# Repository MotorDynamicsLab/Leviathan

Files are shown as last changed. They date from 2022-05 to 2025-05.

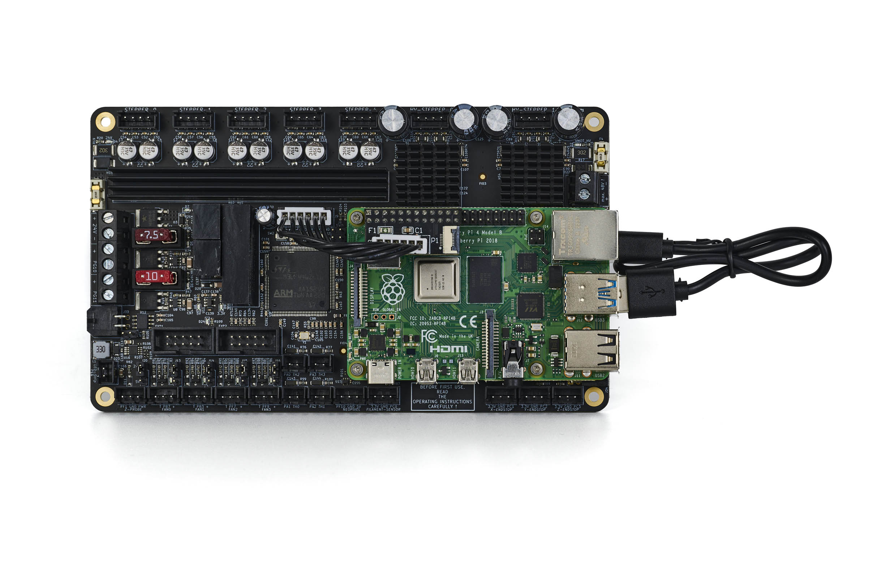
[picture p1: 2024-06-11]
Media/rpi4_usb_installed.jpg

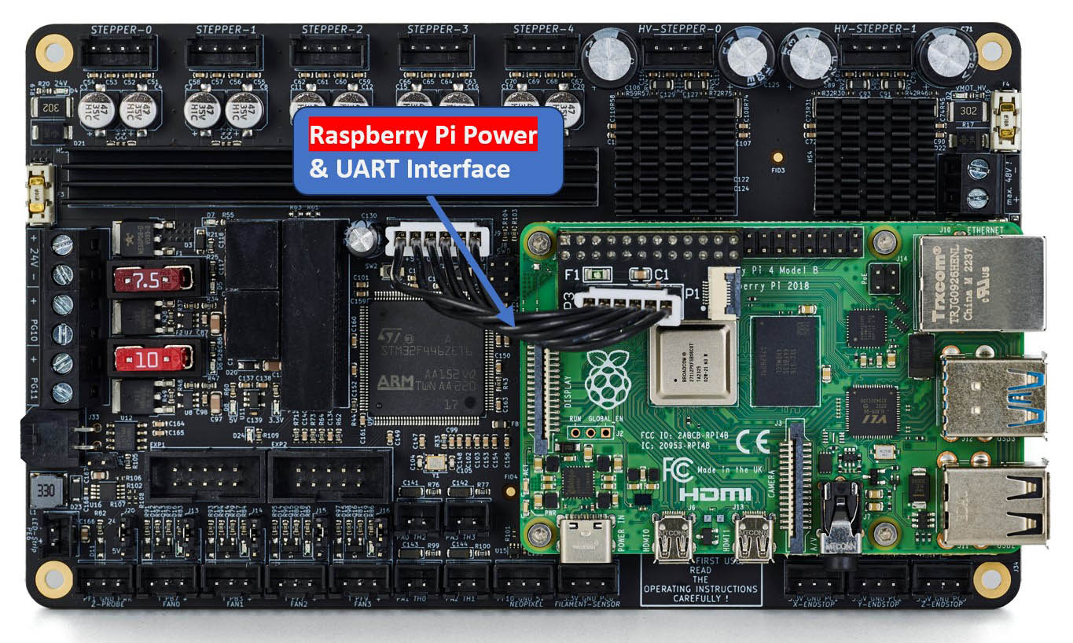
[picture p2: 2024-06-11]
Media/rpi4_installed_UART_labels.jpg

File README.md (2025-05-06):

Leviathan_Mainboard Leviathan Mainboard

# Voron Leviathan
Voron Leviathan is collaboration between JNP and the team at LDO to create a controller board specific for the needs of Voron 3D printers. It features: 
- STM32F446 Microcontroller at 180Mhz clock speed. 
- Reverse polarity protection for main power supply and HV Stepper supply input
- Superior stepper driver cooling (passive)
- Dedicated mounting space for a Raspberry Pi 3,4,5 or Zero 2W
- Dedicated power supply and uart port for Raspberry Pi
- 5x Integrated TMC2209 stepper drivers. 
- 2x Integrated 48V rated TMC5160 stepper drivers. 
- 4x Fan ports with flyback protection, 5V/24V selectable voltage, and tachometer inputs. 
- 4x Thermistor ports with 2k2 ohm pullup resistors. 
- 1x Dedicated LED strip with flicker free dimming down to 1%.
- 1x Neopixel port.
- 1x Hotend power output up to 180W. 
- 1x Hotbed power output up to 240W
- 1x Dedicated Z probe port with selectable voltage and integrated diode.
- 3x Endstop ports and a filament sensor port 

## Setup Guide
https://ldomotion.com/p/guide/VORON-Leviathan-V12

## Electrical Specifications
| Parameter | Symbol |  Min  | Typ | Max | Unit | Comments |
| --- | --- | ----- | ----- | ----- |----- | --- |
| Main Supply Voltage | V<sub>in</sub> | 18 | 24 | 28 |  V | Supply voltage for the entire PCB except for HV stepper drivers |
| HV Stepper Supply Voltage | V<sub>HV</sub> | 24 | 48 | 55 |  V | Supply voltage for the HV stepper drivers |
| RPi Supply Out | I<sub>RPI</sub> | | | 3 |  A | Current rating of Raspberry Power supply output |
| Hotend Current | I<sub>he</sub> | | | 7.5 |  A | Current rating of hotend channel |
| Heatbed Current | I<sub>hb</sub> | | | 10 |  A | Current rating of heatbed channel |
| Fan Current | I<sub>fan</sub> | | | 0.5 |  A | Current rating per fan channel |
| Stepper Current | I<sub>mot</sub> | | | 2 |  A | Current rating of each TMC2209 stepper channel |
| HV Stepper Current | I<sub>hv_mot</sub> | | | 3 |  A | Current rating of each TMC5160 stepper driver |
| Neopixel Current | I<sub>rgb</sub> | | | 0.5 |  A | Current rating Neopixel port |
| LED-Strip Current | I<sub>led</sub> | | 0.35  | |  A | Current rating of LED strip |
| Endstop IO Level | V<sub>stop</sub> | | 3.3 | 5.0 |  V | Logic level of endstop input |
| Filament Sensor IO Level  | V<sub>fil</sub> | | 3.3 | 5.0 |  V | Logic level of filament sensor input |

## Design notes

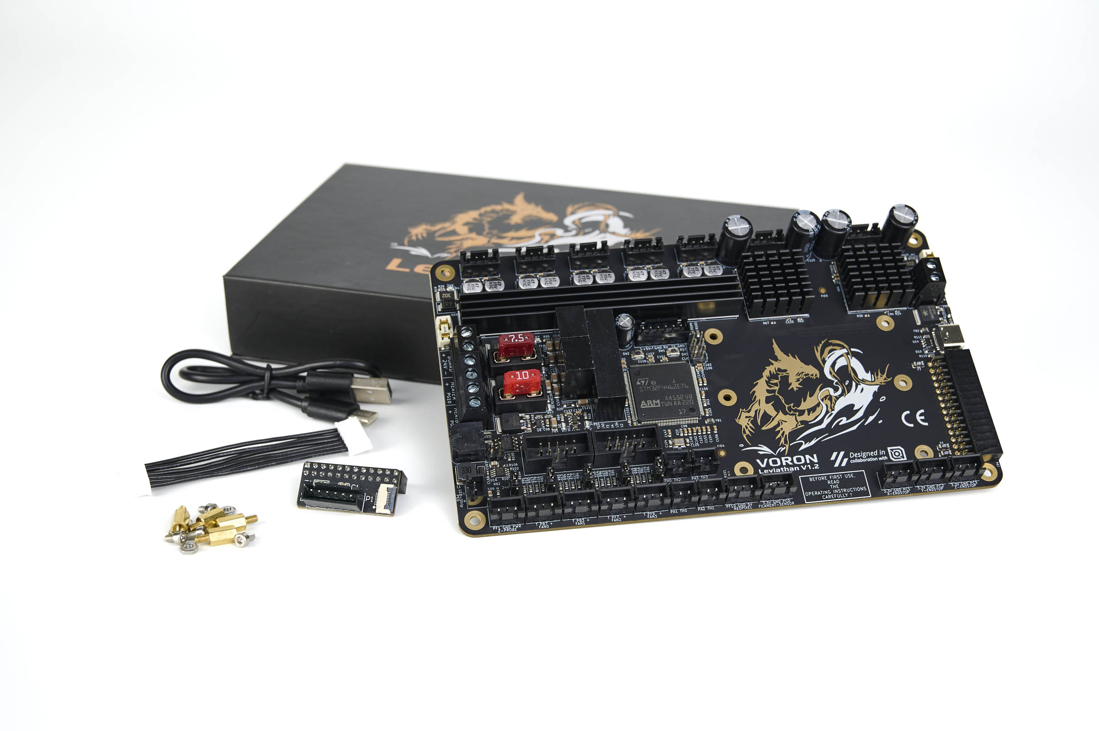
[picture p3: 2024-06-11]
Media/overview.jpg

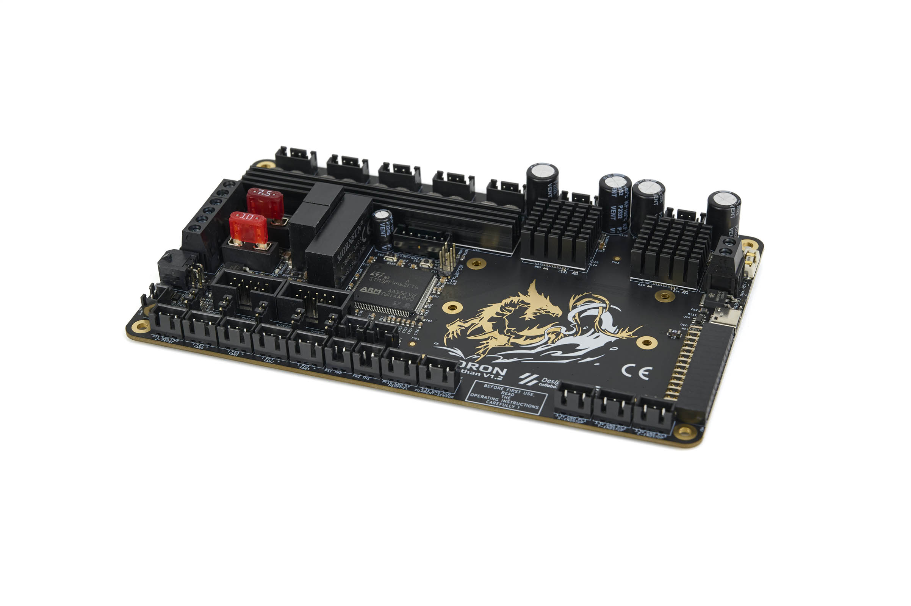
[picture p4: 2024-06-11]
Media/perspective_view.jpg

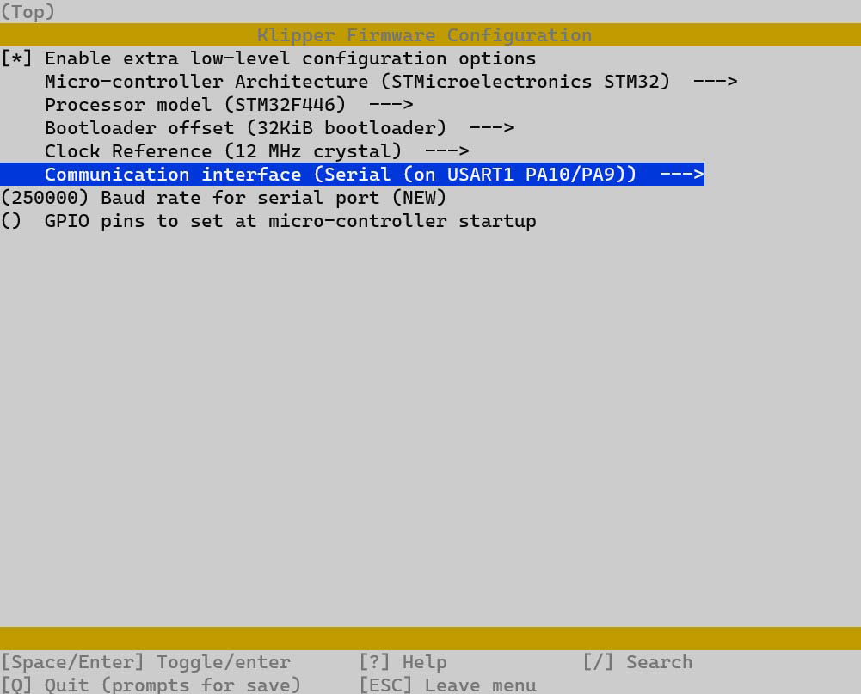
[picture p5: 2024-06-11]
Media/klipper_uart.jpg

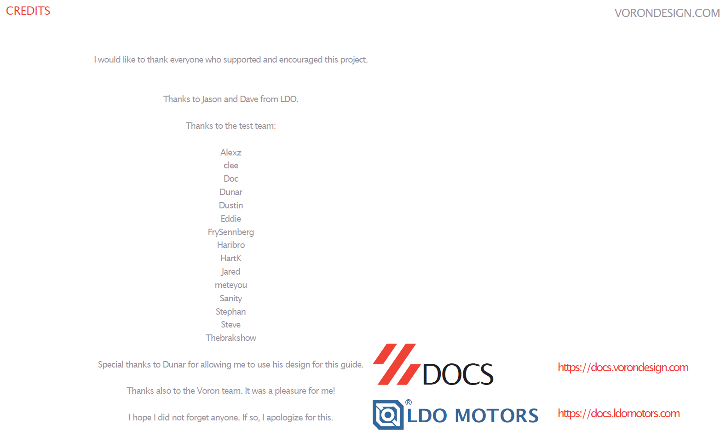
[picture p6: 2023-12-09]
Media/credits.png

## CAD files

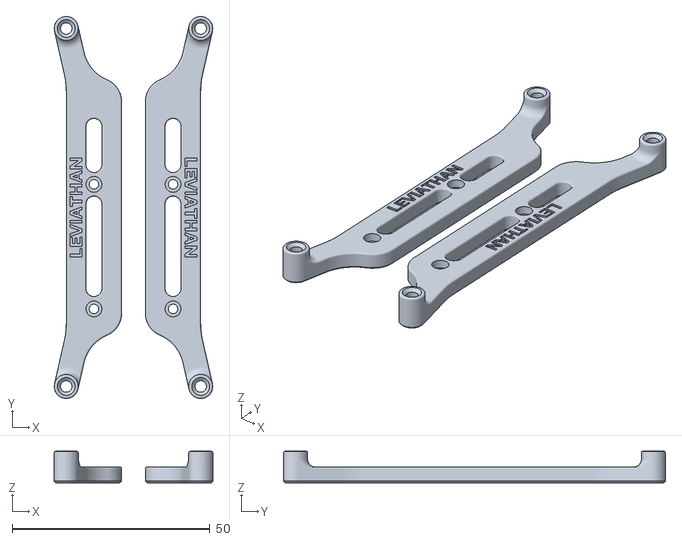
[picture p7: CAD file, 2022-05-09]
STLs/Leviathan_bracket_set.stl
40.1 x 96.6 x 8.00

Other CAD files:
STLs/Leviathan_bracket_set.f3d

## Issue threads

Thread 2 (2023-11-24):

Marlin source

thisiskeithb, 2023-11-24:
Hello!

Keith here from the [Marlin Firmware team](https://github.com/MarlinFirmware/Marlin).

Jason was kind enough to ship over one of these Leviathan boards to add Marlin support, but starting from scratch is fairly involved and I was hoping to collect some more information/files from a board developer. I can create the required pins file based on the [Klipper configs hosted within this repo](https://github.com/MotorDynamicsLab/Leviathan/tree/master/Firmware) and labeling on the board, but I don't have the PlatformIO variant files or build environment details which are crucial to getting it up and running.

We have a few boards with an `STM32F446ZET6` MCU, namely the BTT Octopus Pro V1.0, so I planned to copy those variant files over as a starting point just to see if I can get it going, but I doubt it'll be that easy 😄.

As an example of what I'm after, [here's a PR I put into Marlin](https://github.com/MarlinFirmware/Marlin/pull/23008/files) adding support for a board. These files in particular would be helpful:
- `buildroot/share/PlatformIO/boards/<board>.json`
- `buildroot/share/PlatformIO/variants/<variant>/*`
- Variant details in `ini/stm32f4.ini`.

If you have a working Marlin source, I can get that prepped & ported upstream, but any info would be greatly appreciated!

JNP-1, 2023-11-24:
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

Nice to have you here. I'll have a look at it. I have to set up PlatformIO first.
To be honest, I haven't done anything with Marlin for a long time.
But it shouldn't be a problem.

thisiskeithb, 2023-11-25:
I'm going to close this issue since @meteyou submitted a PR and we're working through the required changes.

Thanks!

Closed 2023-11-25.

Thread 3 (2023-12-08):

Manual Diagram Out of Date (Page 13)

ChrisWhite1985, 2023-12-08:
Please can you update the manual on page 13 to show the latest PCB layout.

Also can you share the PCB Socket Types so we can acquire the correct plugs and include how best to connect the board to RPI?

JNP-1, 2023-12-11:
> Please can you update the manual on page 13 to show the latest PCB layout.
>
> Also can you share the PCB Socket Types so we can acquire the correct plugs and include how best to connect the board to RPI?

Page 13 already shows the current layout (V1.2).
All sockets are of the JST-XH type.
A ready-made cable with adapter board is already included for the Pi power supply.
It is also described here with pictures in the Raspberry Pi Mounting section.
https://www.ldomotion.com/p/guide/VORON-Leviathan-V12

ChrisWhite1985, 2023-12-11:
Ah I can see that Page 13 shows a Raspberry Pi installed on the Leviathan which is where my confusion started. This should be made clear i.e. "Leviathan V1.2 with Raspberry Pi 4 Model B installed". As RPI is not included with the Leviathan board and requires the user to install it seperately?

JNP-1, 2023-12-11:
> Ah I can see that Page 13 shows a Raspberry Pi installed on the Leviathan which is where my confusion started. This should be made clear i.e. "Leviathan V1.2 with Raspberry Pi 4 Model B installed". As RPI is not included with the Leviathan board and requires the user to install it seperately?

To be honest, page 13 is all about the dimensions.
Mounting material is included with the board, the RPi must be installed by the user.

ChrisWhite1985, 2023-12-11:
Sure, having seen the above link with information on how the RPI mounts its much clearer. What type of plug is the CANBUS port as well please, I think this is also not indicated?

Closed 2023-12-11.

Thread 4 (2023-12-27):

no 12v supply for fan headers

TheRealDeathsneeze, 2023-12-27:
The general selection for fans in 12v is much better than with 24v.  Other contemporary boards support 12v  fans. Leviathan should too.

kingnoob1377, 2023-12-28:
Yes, 12V fans are much more common, so not having any 12V port is such a bummer.

JNP-1, 2024-01-02:
Is this about a specific use case?

TheRealDeathsneeze, 2024-01-04:
yes. 12v fans that are not available in 24v or 5v variants. specifically 1U server fans.

JNP-1, 2024-01-05:
424J/2HP from ebmpast are 24V 1U server fans.
https://www.ebmpapst.com/de/en/products/axial-fans/p/424JH.html

TheRealDeathsneeze, 2024-01-10:
I wasnt aware of that option, however it's fairly low flow and somewhat low temperature rating.

a 12v option on the board would open up the selection for fans greatly. Would love to see it on a revision of the board

JNP-1, 2024-01-10:
May I ask what you want to do with a high flow fan on a printer?

CallumRD1, 2024-02-02:
I also miss the 12V fan option on the Leviathan. I have a stash of 12V Noctua electronics fans that I use on printers and the best 4010 part cooling fans for Xol or Blackbird/Archetype toolheads are 12V.

JNP-1, 2024-02-07:
Noctua now also has 24V. Another option would be to use a 24V fan and throttle it via PWM.

CallumRD1, 2024-02-07:
While many 24V fans do exist, that doesn’t remove the utility of having a 12V option. I’m currently forced to run 12V buck converters to get my 12V part cooling and electronics fans to run on Leviathan. It was so much more convenient in my octopus where I could just select 12V output. And these fans don’t exist in 24V configurations, so even if I wanted to replace ~$100 in fans for native Leviathan support, I couldn’t. It’s really obnoxious that such a simple and useful feature was omitted from this board.

JNP-1, 2024-02-07:
The decision did not come from me.

TheRealDeathsneeze, 2024-02-07:
> Adding an option to use 12V could be very simple, assuming 12V is available already and the real-estate on the PCB is available as well. Mellow does it with the Fly Super8 too.

Not to mention since the board has 5160s built in, there needs to be a 12v source on the board anyways.

JNP-1, 2024-02-07:
If someone short-circuits these 12V because a fan is defective, the TMC5160 would also be destroyed during operation. This is the reason why these 12V are not available for other things.

CallumRD1, 2024-02-08:
> The decision did not come from me.

We're not trying to direct any criticism towards you directly, just having a conversation about a feature we feel this product is missing.

I, for one, find this enough of an issue that I'm directing a few people I know away from Leviathan because I know that they require 12V fan support and the hassle of figuring out how to deal with alternative 12V fan control is beyond them.

If having the fans on the same 12V rail as the 5160s is an issue then add a second 12V rail dedicated to fans. I'm not saying it's necessarily easy to implement, but I think it's such an important feature that it is with the effort. I think the Leviathan would be a much more compelling product with it. The Leviathan is so close to being an ideal board for most standard printer configurations that it's a shame to see it undercut by a decision like this.

JNP-1, 2024-02-08:
I will take it into account in the next version.

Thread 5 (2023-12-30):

Unable to update firmware after updating klipper - mainsail

midicdj1000, 2023-12-30:
I just flashed the Leviathan with klipper 11 and then told mainsail to update everything. Now I can't flash new firmware it says it can't find the usb port.

I press sw1 twice and the boot loader led flashed.

Run the command to check it is showing

pi@mainsailos:~ $ ls /dev/serial/by-id/*

/dev/serial/by-id/usb-katapult_stm32f446xx_1B0047000451313133353932-if00

I run the flash command
~/klippy-env/bin/python ~/katapult/scripts/flashtool.py -d /dev/ttyACM0 -f out/klipper.bin

and it gives this error

pi@mainsailos:~/klipper $ ~/klippy-env/bin/python ~/katapult/scripts/flashtool.py -d /dev/ttyACM0 -f out/klipper.bin
ERROR:root:Flash Error
Traceback (most recent call last):
  File "/home/pi/klippy-env/lib/python3.9/site-packages/serial/serialposix.py", line 265, in open
    self.fd = os.open(self.portstr, os.O_RDWR | os.O_NOCTTY | os.O_NONBLOCK)
FileNotFoundError: [Errno 2] No such file or directory: '/dev/ttyACM0'

During handling of the above exception, another exception occurred:

Traceback (most recent call last):
  File "/home/pi/katapult/scripts/flashtool.py", line 543, in run
    serial_dev.open()
  File "/home/pi/klippy-env/lib/python3.9/site-packages/serial/serialposix.py", line 268, in open
    raise SerialException(msg.errno, "could not open port {}: {}".format(self._port, msg))
serial.serialutil.SerialException: [Errno 2] could not open port /dev/ttyACM0: [Errno 2] No such file or directory: '/dev/ttyACM0'

During handling of the above exception, another exception occurred:

Traceback (most recent call last):
  File "/home/pi/katapult/scripts/flashtool.py", line 629, in main
    loop.run_until_complete(sock.run(args.device, args.baud, fpath))
  File "/usr/lib/python3.9/asyncio/base_events.py", line 642, in run_until_complete
    return future.result()
  File "/home/pi/katapult/scripts/flashtool.py", line 545, in run
    raise FlashCanError("Unable to open serial port: %s" % (e,))
FlashCanError: Unable to open serial port: [Errno 2] could not open port /dev/ttyACM0: [Errno 2] No such file or directory: '/dev/ttyACM0'
pi@mainsailos:~/klipper $

midicdj1000, 2024-01-02:
With some help from the klipper discord this command worked

~/klippy-env/bin/python ~/katapult/scripts/flashtool.py -d /dev/serial/by-id/usb-katapult_stm32f446xx_1B0047000451313133353932-if00 -f out/klipper.bin

it needed the full dev device instead of the ttyACM0

camerony, 2024-01-02:
Can I get some more information?  What versions of the RPi are you using?  Also the OS version, Bookworm or Bullseye?

midicdj1000, 2024-01-03:
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

PI 3B+

How do I check for /dev/ttyACM0 ?

camerony, 2024-01-03:
`ls /dev/tty*`

midicdj1000, 2024-01-03:
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

midicdj1000, 2024-01-03:
how do you know what it's allocated to ?
something must have changed between the first flashing and all the upgrades.

midicdj1000, 2024-01-03:
I forgot to show cmdline
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

camerony, 2024-01-03:
That is your USB port, not sure what happened.  But it should work with /dev/ttyACM0, if the Leviathan is the only device plugged in to the Rpi.

midicdj1000, 2024-01-03:
It did work the first time before all the updates

camerony, 2024-01-03:
Does it work now though?  I'll haven't been able to reproduce your issue, since /dev/ttyACM0 exists.

midicdj1000, 2024-01-03:
and it does not program
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

midicdj1000, 2024-01-03:
if I change to ttyACM1 it programs ok
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

camerony, 2024-01-03:
Ok, thanks.  Not sure why you're not getting /dev/ttyACM0 in bootloader mode.  But at least we confirmed it does work, just that it got reassigned as /dev/ttyACM1.     I'll see if can reproduce that.

midicdj1000, 2024-01-03:
it would be a lot easier to use the /dev/serial/by-id/usb-katapult_stm32f446xx_1B0047000451313133353932-if00 with the unique id, you ask to check this is present so why not use it and save any potential problems with the ACM0

camerony, 2024-01-03:
true, I'll add that is a second option.  Thanks for troubleshooting.

midicdj1000, 2024-01-03:
Can you explain the USB, CAN and UART options at the start.
If I am using UART to talk to the PI will this stop me using CAN to connect to a toolhead board ?

I setup with USB to talk to the PI and want to use  CAN connect to a BTT board once I have everthing else setup.

camerony, 2024-01-03:
I suggest you join https://discord.com/channels/692982154577313814/1180911286142369842   for that question.

camerony, 2024-01-03:
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

added addition command option

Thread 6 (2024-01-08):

P1 connector what for?

sergelhr, 2024-01-08:
in ref rpi4_installed.jpg there is a connector with label P1 onto the small power pcb , is for adxl 345 connection ?
Regards
Serge

JNP-1, 2024-01-10:
Exactly.

sergelhr, 2024-01-17:
please update documentation

Closed 2024-01-17.

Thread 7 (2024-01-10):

Can the Leviathan be configured for sensorless homing?

jetcat-bob, 2024-01-10:
Can the Leviathan be configured for sensorless homing?

JNP-1, 2024-01-10:
Of course, the diag pins are specified in the manual (see page 9). No jumpers needed.

JNP-1, 2024-02-07:
Can I close the issue?

jetcat-bob, 2024-02-07:
Yes, please!

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

--

Bob Wilcox

Closed 2024-02-07.

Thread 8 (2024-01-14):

other users

Magneticrob1, 2024-01-14:
are there any other users of this board on here, i have put bootloader and firmware on but cant connect to any external can modules. is there a original bootloader file available anywhere

midicdj1000, 2024-01-16:
I am trying to connect to the EBB36 V1.2 and I think I have the same problem, it only has one can bus ID when it's connected.
I also don't know how to setup the MCU for the can bridge.

midicdj1000, 2024-01-17:
I flashed my EBB board with the stm programmer and I have it working.

Mattang-Tim, 2024-02-05:
I was able to get mine flashed/connected up using the CB1 eMMC with the Pi4B board as my Pi.

JNP-1, 2024-02-07:
> are there any other users of this board on here, i have put bootloader and firmware on but cant connect to any external can modules. is there a original bootloader file available anywhere

Have you also activated the CAN interface under Linux?

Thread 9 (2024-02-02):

usage of tach wire with 5v delta fans results in fan shutting off

TheRealDeathsneeze, 2024-02-02:
When the tachometer pin on a 5 volt 3 wire Delta axial fan is used with any of the fan ports, it results in the fan shutting off instead of spinning and no tachometer output is given.

I had initially thought that there was an error with the listing for these fans, as the tachometer wire is blue instead of the typical yellow. However, when plugged into another known working device, the fan behaves as expected.

TheRealDeathsneeze, 2024-02-02:
Of note is that a 4020 12v Delta 4 wire fan(model THA0412AD) I have on hand does function as expected. The tested fan not working as expected is ASB02505SHA-AY6B. See attached datasheets for both fans.
[ASB02505SHA-AY6B.pdf](https://github.com/MotorDynamicsLab/Leviathan/files/14144702/ASB02505SHA-AY6B.pdf)
[THA0412AD.pdf](https://github.com/MotorDynamicsLab/Leviathan/files/14144703/THA0412AD.pdf)

JNP-1, 2024-02-03:
I looked at both data sheets and could not see any difference in the tach pin.
Even if you connect the tach pin to GND, the fan must work.
On Leviathan, the tach pin is also "decoupled" and protected with a diode.
This must have another cause.

TheRealDeathsneeze, 2024-02-07:
the working fan is 12v. As best as I can tell the tach is using 15v logic.
the non working fan is 5v. I'm guessing using 5v logic? Either way, it functions as expected when plugged into an endstop port on an ebb36.

See attached reference images.

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

TheRealDeathsneeze, 2024-02-07:
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

JNP-1, 2024-02-07:
The tach output of a fan is an open collector output.
This means that the level depends on the signal from the pull-up resistor (to which voltage it is connected) and not on the operating voltage of the fan.
In the case of Leviathan, this is a 3.3V signal.

TheRealDeathsneeze, 2024-02-07:
oh so in this case, perhaps the reason it does not function is expected is due to the 3.3v pullup not being a 5v pullup?

This is a fair bit outside of the scope of my knowledge, is there a way I could easily test to see if this is the root of the problem?

JNP-1, 2024-02-07:
The MCU only needs a 3.3V signal to recognize the tacho.
So I don't understand why it shouldn't work with a 5V fan.

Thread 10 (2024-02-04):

Will not boot to DFU mode.

Killajoedotcom, 2024-02-04:
No matter what combination of buttons I try, I cannot get the board to boot to DFU mode. I have tried on 24v and USB power. Also tried holding the boot button before connecting the USB and still nothing. I'm starting to think my board is dead.

Closed 2024-02-04.

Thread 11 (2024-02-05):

PI4B don't  boot with power suplly from leviathan board and usb connected

sergelhr, 2024-02-05:
I've got  an issue with the integrated power supply, no boot if a toolboard is connected via pi4b usb!
if a use an official 3a psu connected to the usb-c no issue pi4b boot and eveything is working (leviathan and toolboard btt sb2209)
To boot from leviathan integrated power supply i need to disconect then reconnect the usb toolboard!
weak integrated power supply?

sergelhr, 2024-02-06:
Might be related to the 24v toolhead, feed directly from my 24v psu, what the connector type/part number of the can/24v board connector.
i don't reminder if the male connector  4 pins was provided, most probably lost!

sergelhr, 2024-02-06:
finally is seems to be related to 24v of my toolboard, with the 24v feed from the can/24v, no boot issue , now what the max amperage available from that connector ? F3 10A?

sergelhr, 2024-02-06:
NO; might be my raspi reaching his EOF, to be confirmed looking for an another one

sergelhr, 2024-02-06:
look like k7805-3ar3 seems faulty, using an extenal 5v psu no more issue

JNP-1, 2024-02-06:
The supply for the Pi delivers 3A.
The BTT SB2209 is a CAN board, have you tried to operate it via USB instead of CAN?

JNP-1, 2024-02-07:
I have already tested Leviathan with Pi3/4/5 without any problems.
The integrated power supply for the Pi was never a problem.
However, I use CAN bus on my toolhead.
So the only difference is the interface, CAN bus instead of USB.

sergelhr, 2024-02-07:
I don't no if  there a sort of  Power Delivery negotiation for the RPI4 USB C, my meanwell PSU is set to 5.1v and it is connected via the small pcb provided by LDO

JNP-1, 2024-02-07:
I would not make the connection to the toolhead via USB without a protective circuit on the USB port.
Many people have already destroyed their Pi with this.
I therefore suspect that the cause lies elsewhere.

sergelhr, 2024-02-08:
I will give a try to this product from waveshare Industrial Grade USB HUB, Extending 4x USB 2.0 Ports.
For info i ran this toolhead for a year without any issue from the usb port cm4/Manta 8p

sergelhr, 2024-02-10:
strangely with a PI 5, from internal psu no boot issue and now all usb are passing through waveshare Industrial Grade USB HUB. My PI4b was both very old few years might be related?

Closed 2024-03-11.

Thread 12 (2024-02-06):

Limited capacity LED driver for strip lighting?

jetcat-bob, 2024-02-06:
My LDO Voron 2.4 kit came with 2 strip LEDs for the chamber light. Their combined current requirement is 580ma @ 24v. The Leviathan has a limit of 350ma (LM3407MY). Is there a suggestion for a replacement LED strip that would be compatible with half the current of the supplied strip? It would be nice to have the same brightness. Maybe a more capable driver in the future would be nice......
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

JNP-1, 2024-02-06:
Perhaps the LED strip is too long. In my printer, I have a total of 36 LEDs (2x18) on the port.
Was the V2.4 an LDO kit?

jetcat-bob, 2024-02-06:
Yes it's a Voron 2.4 LDO kit. Two strips with 18 LEDs each. Each strip
pulls 280ma.

I was considering using a fan port on the Leviathan but I did find a lower
power LED strip that would work. 170ma per strip of 18. Not as bright
however.

I like the idea of having a constant current source for the lighting but
maybe on V2 consider a higher output device ;).

Bob Wilcox

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

JNP-1, 2024-02-07:
Then we both have the same LED strips, my printer is also an LDO kit.
With a constant current source, the output voltage is regulated to achieve the 350mA.
In my case I get 22.5V, the two LED strips are connected in parallel (with the included little PCB in the Kit).
Is it the same for you?

jetcat-bob, 2024-02-07:
Measuring with my DVM and not the iffy power supply, I get 20.8V @ 353ma.
Full brightness @ 24V is 510 ma. There is a difference but I can live with
it. Compared to my other Voron 2.4 that has 3 strips of 18 LEDs (24V @
700ma) on an Octopus fan port, it's pretty dim.

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

--

Bob Wilcox

JNP-1, 2024-02-07:
It is clear that the current increases slightly at 24V. At 28V they are even brighter ;-)

ccatlett1984, 2024-02-08:
Just run positive and negative to the PSU, only the "signal" wire needs to be on the pin. if 3 wire.
Or use the spare heater output for them.

jetcat-bob, 2024-02-08:
I don't have a spare fan output but there is a spare heater. I'll look into
that possibility. Thanks for the suggestion!

Bob Wilcox

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

CallumRD1, 2024-02-08:
I’m also surprised at how low of a current the LED port is regulated to. My lights want to draw far more current than the header will output. It’s a very convenient port but isn’t usable for me due to the low brightness of LEDs connected to it. When I use a heater output with unregulated 24V the LEDs are far brighter. I’d have much preferred an unregulated LED header.

ccatlett1984, 2024-02-08:
You can use [output_pin] for that pin, and be able to control the
brightness.

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

JNP-1, 2024-02-08:
If you connect the LED strips in series, they should be brighter.

CallumRD1, 2024-02-08:
I can't. I'm using Daylight on a Stick and Matchlight on a Stick. They're designed to be run inline off of 24V.

ccatlett1984, 2024-02-09:
for those, you run the 24v directly to the psu, and the "data" pin to the
neopixel header on the board.

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

CallumRD1, 2024-02-09:
> for those, you run the 24v directly to the psu, and the "data" pin to the neopixel header on the board.
> […](#)
> On Thu, Feb 8, 2024 at 6:21 PM CallumRD1 ***@***.***> wrote: I can't. I'm using Daylight on a Stick and Matchlight on a Stick. They're designed to be run inline off of 24V. — Reply to this email directly, view it on GitHub <[#12 (comment)](https://github.com/MotorDynamicsLab/Leviathan/issues/12#issuecomment-1935085487)>, or unsubscribe <https://github.com/notifications/unsubscribe-auth/ABY4LWIXD52U3GRWHATZAXLYSVMXDAVCNFSM6AAAAABC4LNVDWVHI2DSMVQWIX3LMV43OSLTON2WKQ3PNVWWK3TUHMYTSMZVGA4DKNBYG4> . You are receiving this because you commented.Message ID: ***@***.***>

You have no idea what you’re talking about. These are not now pixels and have no control wire. They’re 24V white led strips with two pins: 24V and ground. They’re designed (like most white lite led strips for this kind of application) to take in straight, non current regulated 24V and daisy chain in parallel so you can run many of them inline.

jetcat-bob, 2024-02-09:
The LED strips are 2 wire. They are not addressable. For my case, I'll use
the the tool head heater output for the LEDs since the printer uses a
canbus driver board. The heater has plenty of current capability for making
the printer glow very brightly...

Bob Wilcox

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

ccatlett1984, 2024-02-09:
> > for those, you run the 24v directly to the psu, and the "data" pin to the neopixel header on the board.
>
> You have no idea what you’re talking about. These are not neopixels and have no control wire. They’re 24V white led strips with two pins: 24V and ground. They’re designed (like most white light led strips for this kind of application) to take in straight, non current regulated 24V and daisy chain in parallel so you can run many of them inline.

I have a set that have the 3 pin connectors. Didn't realize they had 2 pin variants..
No need to be snobby about it.

Hecatron, 2025-06-22:
Stumbled across the issue myself just now, after the LED driver popped on the board
U15 / LM3407MY
I didn't think to check the current draw on the driver vs the led strip since both came in the LDO kit

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

JNP-1, 2025-06-23:
> Edit sorry I think this is a different problem The bust IC is the neopixel driver U15 / LM3407MY but I didn't have that plugged in I think what's happened in my case is the 5V rail might have developed a 78 ohm short to ground Which in turn might have spiked the 5V rail causing that IC (and possibly lots of others) to go boom, will check the 5V rail on my new one to see if it has a similar load
>
> 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

All voltage regulators on Leviathan are short-circuit protected.
I therefore do not believe that this is the cause.
U15 (74LVC1G17GW) is a 5V driver for the data line of the Neopixel.
Can you please open a new issue because it has nothing to do with the LED driver, thank you.

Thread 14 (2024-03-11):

pwm fan

sergelhr, 2024-03-11:
As there is no dedicated port for pwm fan with four pins, i would like to know if it is possible to use PG10 to control my fan ?
https://noctua.at/en/nf-f12-industrialppc-24v-3000-sp-ip67-pwm
I believe PG10 is 24v and i need 5v!

JNP-1, 2024-03-11:
PG10 is a switched GND. PF10 is a 5V output (Neopixel).
All fan outputs have a switched GND.

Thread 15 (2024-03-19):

Amp limit of rpi connector

HaernCalistinson, 2024-03-19:
Could you please document the amp limit of the rpi connector somewhere?

Is it 3a limiting use to rpi 4, or is it 5a allowing for use of an rpi5?

JNP-1, 2024-03-20:
The current is limited to 3A by the DCDC converter.
However, I have also successfully tested the RPi5 and it works exactly the same way.
I had not received an undervoltage warning from RPi3-RPi5.

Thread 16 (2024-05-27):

Switching to DFU mode is no longer possible

MarkusNiewoehner, 2024-05-27:
For reasons unknown to me I can no longer switch to DFU mode. The Levithan is installed in a working printer and no other USB devices are connected

Here is the dmesg output after pressing the boot and reset buttons as described in the instructions:

biqu@Trident250:~$ dmesg -HW
[May27 12:31] usb 7-1: USB disconnect, device number 4
[  +0.000688] [dhd] CFG80211-ERROR) wl_cfg80211_netdev_notifier_call : wdev null. Do nothing
[  +0.000228] gs_usb 7-1:1.0 can0: Couldn't shutdown device (err=-19)
[  +0.000281] [dhd] CFG80211-ERROR) wl_cfg80211_netdev_notifier_call : wdev null. Do nothing
[  +0.003354] [dhd] CFG80211-ERROR) wl_cfg80211_netdev_notifier_call : wdev null. Do nothing
[  +0.868004] usb 7-1: new full-speed USB device number 5 using xhci-hcd
[  +0.144559] usb 7-1: New USB device found, idVendor=1d50, idProduct=606f, bcdDevice= 0.00
[  +0.000008] usb 7-1: New USB device strings: Mfr=1, Product=2, SerialNumber=3
[  +0.000004] usb 7-1: Product: stm32f446xx
[  +0.000003] usb 7-1: Manufacturer: Klipper
[  +0.000004] usb 7-1: SerialNumber: 350033000A51313133353932
[  +0.001290] gs_usb 7-1:1.0: Configuring for 1 interfaces
[  +0.000185] [dhd] CFG80211-ERROR) wl_cfg80211_netdev_notifier_call : wdev null. Do nothing
[  +0.000323] [dhd] CFG80211-ERROR) wl_cfg80211_netdev_notifier_call : wdev null. Do nothing
[  +0.146798] [dhd] CFG80211-ERROR) wl_cfg80211_netdev_notifier_call : wdev null. Do nothing
[  +0.000802] IPv6: ADDRCONF(NETDEV_UP): can0: link is not ready
[  +0.000010] [dhd] CFG80211-ERROR) wl_cfg80211_netdev_notifier_call : wdev null. Do nothing
[  +0.000046] IPv6: ADDRCONF(NETDEV_CHANGE): can0: link becomes ready
[  +0.000004] [dhd] CFG80211-ERROR) wl_cfg80211_netdev_notifier_call : wdev null. Do nothing
[  +0.005909] [dhd] CFG80211-ERROR) wl_cfg80211_netdev_notifier_call : wdev null. Do nothing

JNP-1, 2024-06-04:
Do you have an STLink V2? You could use this to check whether the MCU is still accessible via the SWD interface.

MarkusNiewoehner, 2024-06-04:
Yes, but I've never used it before. I'll see if I can try that one day. I was now able to flash the Levi with the current klipper via catapult.

JNP-1, 2024-06-04:
Does the 3.3V LED light up when the board is powered?

MarkusNiewoehner, 2024-06-04:
In 24V operation or 5V USB? I can check tomorrow.

JNP-1, 2024-06-04:
In 24V operation.

MarkusNiewoehner, 2024-06-05:
> Does the 3.3V LED light up when the board is powered?

yes, she does

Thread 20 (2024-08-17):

Provision the Leviathan over SWD?

Poofjunior, 2024-08-17:
The Leviathan has a SWD header with a RESET pin exposed.

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

In theory, it should be possible to flash the bootloader *and* firmware to the Leviathan from a Pi4/5 using OpenOCD and by plugging in the the `SWD`, `SWDIO`, and `RESET` pins to reserved GPIO pins on the Pi4/5.

The result is that we could write an all-in-one script that flashes the bootloader and firmware without requiring that the user push a sequence of buttons on the hardware itself.

This would also ask the user would to plug in another cable (or set of cables) for now, but a future header board could expose these pins or include a dedicated cable.

## References
* [Raspberry Pi 4 OpenOCD GPIO configuration](https://gist.github.com/urish/4d002caa3311986552b11a363a2ddd61)
* [Adafruit OpenOCD on the Pi3 Tutorial](https://cdn-learn.adafruit.com/downloads/pdf/programming-microcontrollers-using-openocd-on-raspberry-pi.pdf)
  * Note that the specified Pi GPIO pins are for the Pi3.

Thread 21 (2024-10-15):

Support for encoded Close-Loop Steppers?

jhox616, 2024-10-15:
I found this board due to its x2 48v stepper driver "ports".

I am looking to put a NEMA 23 or Nema 17 Closed-Loop (with encoder) into my Voron 2.4

Does this board support encoder feedback or if not how would I make it compatible?

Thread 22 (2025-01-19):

5 V rail can't be 5 V

dead-lock-ed, 2025-01-19:
There are reports of 5 V fan and accessory rail (+5V net) outputting around 4,7 V.
This issue can be tracked back to the PCB, where the output of buck converter K7805-2003 (PS3 on schematic) isn't fed directly to the 5 V rail, instead it has to go through a BAT60A (D20) diode.
At room temperature it exhibits around 0,3 V forward voltage at rated output current of the regulator, which can explain the lower than optimal output voltage.
This is too low voltage for many 5 V devices to operate, which greatly reduces the usability of the mainboard.
I attach a screenshot of the schematic showcasing the problematic region 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

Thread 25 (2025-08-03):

Firmware configuration differences for 1.3

Hecatron, 2025-08-03:
It may be worth noting in the online documentation that there are two changes to make for the 1.3 version of the boards

  * Processor mode:
    * 1.2 Board: STM32F446
    * 1.3 Board: STM32H743

  * Clock Reference:
    * 1.2 Board: 12 MHz
    * 1.3 Board: 25 MHz

JNP-1, 2025-08-11:
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

https://ldomotion.com/p/guide/VORON-Leviathan-V13

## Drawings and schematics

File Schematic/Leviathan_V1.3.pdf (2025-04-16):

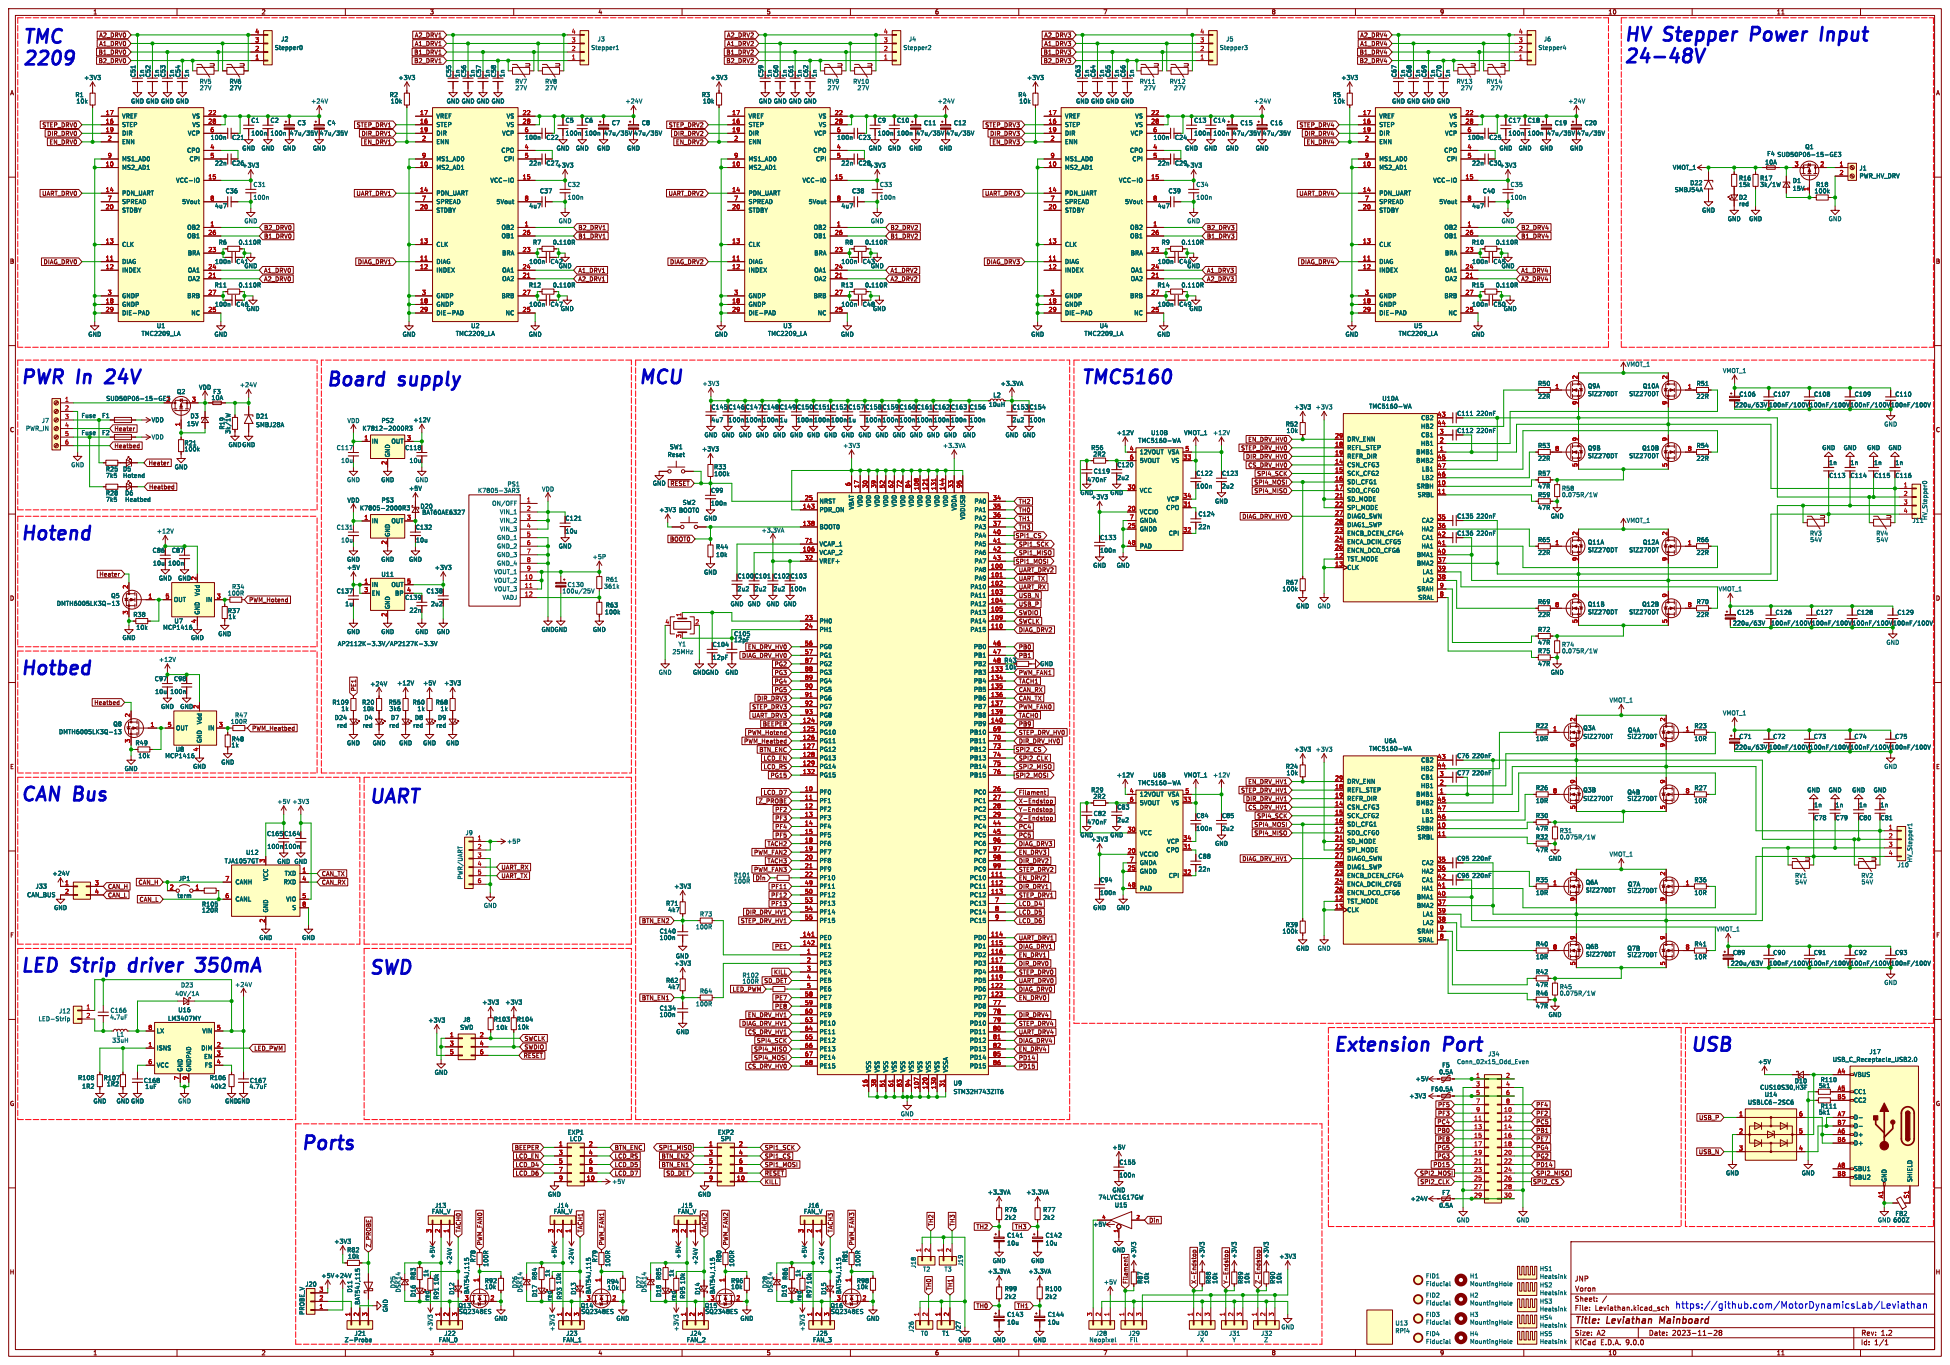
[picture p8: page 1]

J5 Stepper3 C65 1nC66 1n GND GND C64 1n GND GND

6 VDD 17 VDD 30 VSS 16 VDD 39 VSS 38 VDD 52 VSS 51 VDD 62 VSS 61 VDD 72 VSS 83 VDD 84 VSS 94 VDD 108 VSS 107 VDD 121 VSS 120 VDD 131 VSS 130 VDD 144 VSSA 31 VDDA 33 VDDUSB 95 PA0 34 PA1 35 PA2 36 PA3 37 PA4 40 PA5 41 PA6 42 PA7 43 PA8 100 PA9 101 PA10 102 PA11 103 PA12 104 PA13 105 PA14 109 PA15 110 PB0 46 PB1 47 PB2 48 PB3 133 PB4 134 PB5 135 PB6 136 PB7 137 PB8 139 PB9 140 PB10 69 PB11 70 PB12 73 PB13 74 PB14 75 PB15 76 PC0 26 PC1 27 PC2 28 PC3 29 PC4 44 PC5 45 PC6 96 PC7 97 PC8 98 PC9 99 PC10 111 PC11 112 PC12 113 PC13 7 PC14 8 PC15 9 PD0 114 PD1 115 PD2 116 PD3 117 PD4 118 PD5 119 PD6 122 PD7 123 PD8 77 PD9 78 PD10 79 PD11 80 PD12 81 PD13 82 PD14 85 PD15 86 U9STM32H743ZIT6

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

4 OUT 5 U7 MCP1416 GND GND GND GND GND

4 OUT 5 GND GND GND GND GND

VIN 5 DIM 2 EN 3 FS 4 GNDPAD

HS1 Heatsink HS4 Heatsink HS2 Heatsink HS3 Heatsink H2 MountingHole H1 MountingHole
FID3 Fiducial FID1 Fiducial FID2 Fiducial

JNP
File: Leviathan.kicad_sch Sheet: / Voron

https://github.com/MotorDynamicsLab/Leviathan

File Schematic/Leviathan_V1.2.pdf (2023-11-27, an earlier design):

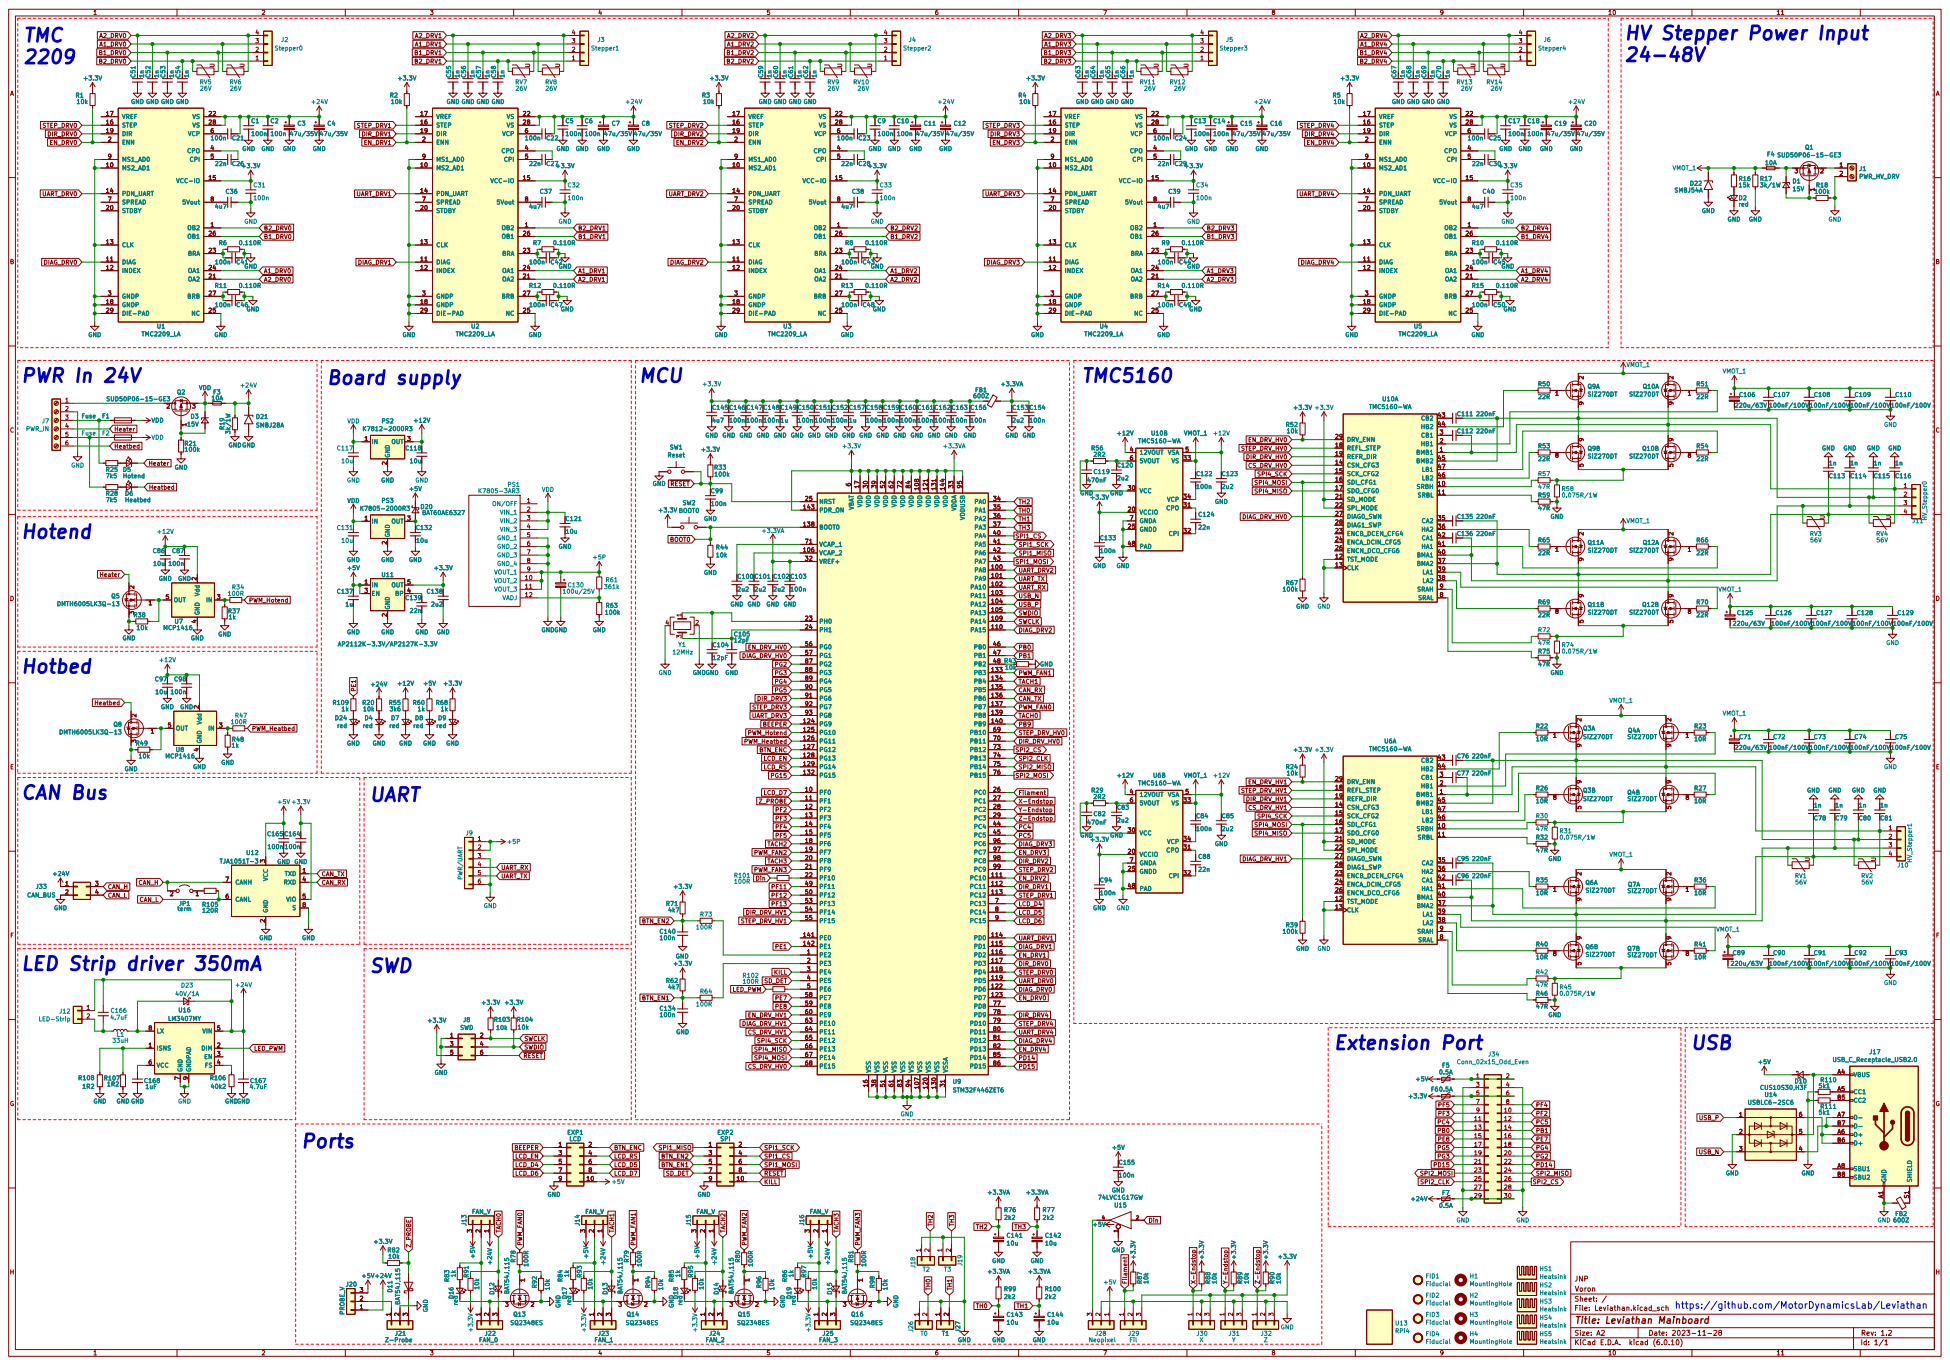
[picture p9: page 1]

GND GND

2 OUT 3 VDD GND GND

2 EN 3 BP 4 OUT 5 GND

3 RXD 4 VIO 5 CANL 6 CANH 7 S

https://github.com/MotorDynamicsLab/Leviathan

Id: 1/1 Title: Leviathan Mainboard

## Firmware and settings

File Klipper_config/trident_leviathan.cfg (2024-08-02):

# This file contains common pin mappings for the Voron Leviathan V1.1
# To use this config, the firmware should be compiled for the STM32F446 with "No bootloader"
# Enable "extra low-level configuration options" and select the "12MHz crystal" as clock reference

# See docs/Config_Reference.md for a description of parameters.

## Voron Design VORON Trident 250/300/350mm Leviathan V1.1 config

## *** THINGS TO CHANGE/CHECK: ***
## MCU paths                            [mcu] section
## Thermistor types                     [extruder] and [heater_bed] sections - See https://www.klipper3d.org/Config_Reference.html#common-thermistors for common thermistor types
## Z Endstop Switch location            [safe_z_home] section
## Homing end position                  [gcode_macro G32] section
## Z Endstop Switch  offset for Z0      [stepper_z] section
## Probe points                         [quad_gantry_level] section
## Min & Max gantry corner postions     [quad_gantry_level] section
## PID tune                             [extruder] and [heater_bed] sections
## Probe pin                            [probe] section
## Fine tune E steps                    [extruder] section

[mcu]
##  Obtain definition by "ls -l /dev/serial/by-id/" then unplug to verify
##--------------------------------------------------------------------
serial: /dev/serial/by-id/{REPLACE WITH YOUR SERIAL}
restart_method: command
##--------------------------------------------------------------------

[printer]
kinematics: corexy
max_velocity: 300  
max_accel: 10000
max_z_velocity: 15          #Max 15 for 12V TMC Drivers, can increase for 24V
max_z_accel: 350
square_corner_velocity: 5.0

#####################################################################
#   X/Y Stepper Settings
#####################################################################

##  B Stepper - Left
##  Connected to HV STEPPER 0
##  Endstop connected to X-ENDSTOP
[stepper_x]
step_pin: PB10
dir_pin: !PB11
enable_pin: !PG0
rotation_distance: 40
microsteps: 32
full_steps_per_rotation:400  #set to 200 for 1.8 degree stepper
endstop_pin: PC1
position_min: 0
##--------------------------------------------------------------------

##  Uncomment below for 250mm build
#position_endstop: 250
#position_max: 250

##  Uncomment for 300mm build
#position_endstop: 300
#position_max: 300

##  Uncomment for 350mm build
#position_endstop: 350
#position_max: 350

##--------------------------------------------------------------------
homing_speed: 25   #Max 100
homing_retract_dist: 5
homing_positive_dir: true

##  Make sure to update below for your relevant driver (2209 or 5160)
[tmc5160 stepper_x]
cs_pin: PE15
spi_bus: spi4
#diag0_pin: ^!PG1
interpolate: false
run_current: 0.8
sense_resistor: 0.075
stealthchop_threshold: 0

##  A Stepper - Right
##  Connected to HV STEPPER 1
##  Endstop connected to Y-ENDSTOP
[stepper_y]
step_pin: PF15
dir_pin: !PF14
enable_pin: !PE9
rotation_distance: 40
microsteps: 32
full_steps_per_rotation:400  #set to 200 for 1.8 degree stepper
endstop_pin: PC2
position_min: 0
##--------------------------------------------------------------------

##  Uncomment for 250mm build
#position_endstop: 250
#position_max: 250

##  Uncomment for 300mm build
#position_endstop: 300
#position_max: 300

##  Uncomment for 350mm build
#position_endstop: 350
#position_max: 350

##--------------------------------------------------------------------
homing_speed: 25  #Max 100
homing_retract_dist: 5
homing_positive_dir: true

##  Make sure to update below for your relevant driver (2209 or 5160)
[tmc5160 stepper_y]
cs_pin: PE11
spi_bus: spi4
#diag0_pin: ^!PE10
interpolate: false
run_current: 0.8
sense_resistor: 0.075
stealthchop_threshold: 0
 
#####################################################################
#   Z Stepper Settings
#####################################################################

## Z0 Stepper - Front Left
##  Connected to STEPPER 0
##  Endstop connected to Z-ENDSTOP
[stepper_z]
step_pin: PD4
dir_pin: PD3
enable_pin: !PD7
# Rotation Distance for TR8x8 = 8, TR8x4 = 4, TR8x2 = 2
# rotation_distance: 8  
microsteps: 32
endstop_pin: PC3
##  Z-position of nozzle (in mm) to z-endstop trigger point relative to print surface (Z0)
##  (+) value = endstop above Z0, (-) value = endstop below
##  Increasing position_endstop brings nozzle closer to the bed
##  After you run Z_ENDSTOP_CALIBRATE, position_endstop will be stored at the very end of your config
position_endstop: -0.5
##--------------------------------------------------------------------

##  Uncomment below for 250mm build
#position_max: 230

##  Uncomment below for 300mm build
#position_max: 280

##  Uncomment below for 350mm build
#position_max: 330

##--------------------------------------------------------------------
position_min: -5
homing_speed: 8
second_homing_speed: 3
homing_retract_dist: 3

##  Make sure to update below for your relevant driver (2209 or 5160)
[tmc2209 stepper_z]
uart_pin: PD5
#diag_pin: ^!PD6
interpolate: false
run_current: 0.8
sense_resistor: 0.110
stealthchop_threshold: 0

##  Z1 Stepper - Rear Center
##  Connected to STEPPER 1
[stepper_z1]
step_pin: PC12
dir_pin: PC11
enable_pin: !PD2
# Rotation Distance for TR8x8 = 8, TR8x4 = 4, TR8x2 = 2
# rotation_distance: 8  
microsteps: 32

##  Make sure to update below for your relevant driver (2209 or 5160)
[tmc2209 stepper_z1]
uart_pin: PD0
#diag_pin: ^!PD1
interpolate: false
run_current: 0.8
sense_resistor: 0.110
stealthchop_threshold: 0

##  Z2 Stepper - Front Right
##  Connected to STEPPER 2
[stepper_z2]
step_pin: PC9
dir_pin: PC8
enable_pin: !PC10
# Rotation Distance for TR8x8 = 8, TR8x4 = 4, TR8x2 = 2
# rotation_distance: 8  
microsteps: 32

##  Make sure to update below for your relevant driver (2209 or 5160)
[tmc2209 stepper_z2]
uart_pin: PA8
#diag_pin: ^!PA15
interpolate: false
run_current: 0.8
sense_resistor: 0.110
stealthchop_threshold: 0

#####################################################################
#   Extruder
#####################################################################

##  Connected to STEPPER 0
##  Heater - HEATER
##  Thermistor - TH0
[extruder]
step_pin: PD10
dir_pin: PD9
enable_pin: !PD13
##  Update value below when you perform extruder calibration
##  If you ask for 100mm of filament, but in reality it is 98mm:
##  rotation_distance = <previous_rotation_distance> * <actual_extrude_distance> / 100
##  22.6789511 is a good starting point
rotation_distance: 22.6789511   #Bondtech 5mm Drive Gears
##  Update Gear Ratio depending on your Extruder Type
##  Use 50:10 for Stealthburner/Clockwork 2
##  Use 50:17 for Afterburner/Clockwork (BMG Gear Ratio)
##  Use 80:20 for M4, M3.1
gear_ratio: 50:10               #BMG Gear Ratio
microsteps: 32
full_steps_per_rotation: 200    #200 for 1.8 degree, 400 for 0.9 degree
nozzle_diameter: 0.400
filament_diameter: 1.75
heater_pin: PG10
## Check what thermistor type you have. See https://www.klipper3d.org/Config_Reference.html#common-thermistors for common thermistor types.
## Use "Generic 3950" for NTC 100k 3950 thermistors
#sensor_type:
sensor_pin: PA1 #TH0
pullup_resistor: 2200
min_temp: 10
max_temp: 270
max_power: 1.0
min_extrude_temp: 170
control = pid
pid_kp = 26.213
pid_ki = 1.304
pid_kd = 131.721
##  Try to keep pressure_advance below 1.0
#pressure_advance: 0.05
##  Default is 0.040, leave stock
#pressure_advance_smooth_time: 0.040

##  E0 on MOTOR6
##  Connected to STEPPER 4
[tmc2209 extruder]
uart_pin: PD11
interpolate: false
run_current: 0.5
sense_resistor: 0.110
stealthchop_threshold: 0


#####################################################################
#   Bed Heater
#####################################################################

[heater_bed]
##  SSR Pin - HEATBED
##  Thermistor - TH1
heater_pin: PG11
## Check what thermistor type you have. See https://www.klipper3d.org/Config_Reference.html#common-thermistors for common thermistor types.
## Use "Generic 3950" for Keenovo heaters
#sensor_type:
sensor_pin: PA2
pullup_resistor: 2200
##  Adjust Max Power so your heater doesn't warp your bed. Rule of thumb is 0.4 watts / cm^2 .
max_power: 0.6
min_temp: 0
max_temp: 120
control: pid
pid_kp: 58.437
pid_ki: 2.347
pid_kd: 363.769

#####################################################################
#   Probe
#####################################################################

[probe]
##  Inductive Probe
##  Connected to Z-PROBE
##  This probe is not used for Z height, only Quad Gantry Leveling
pin: ^PF1
x_offset: 0
y_offset: 25.0
z_offset: 0
speed: 10.0
samples: 3
samples_result: median
sample_retract_dist: 3.0
samples_tolerance: 0.006
samples_tolerance_retries: 3

#####################################################################
#   Fan Control
#####################################################################
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

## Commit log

2022-05-06 add voron2_leviathan_v1.1.cfg
    [voron2_leviathan_v1.1.cfg]
2022-05-06 add trident_leviathan_v1.1.cfg
    [trident_leviathan_v1.1.cfg]
2022-05-09 Added Leviathan DIN mount.
    [Leviathan_bracket_set.f3d, Leviathan_bracket_set.stl]
2022-05-13 fix incorrect z rotation distance in Firmware/trident_leviathan_v1.1.cfg
    [trident_leviathan_v1.1.cfg]
2023-11-21 add PCB image to README.md
2023-11-26 Adding KiCad files, step file, config files and user manual
    [Leviathan.kicad_sch, Leviathan.sch, trident_leviathan_v1.1.cfg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]
2023-11-27 Filament sensor added
    [trident_leviathan_v1.2.cfg, voron2_leviathan_v1.2.cfg]
2023-11-27 Updated KiCad files, schematic exported to pdf file
    [Leviathan.kicad_sch]
2023-11-27 update cycle_time for led-strip
    [trident_leviathan_v1.2.cfg, voron2_leviathan_v1.2.cfg]
2023-12-11 Dir pins corrected in voron2_leviathan_v1.2.cfg
    [voron2_leviathan_v1.2.cfg]
2024-01-14 Change cycle_time to 0.00025 for LED-Strip
    [trident_leviathan_v1.2.cfg, voron2_leviathan_v1.2.cfg]
2024-07-22 fix cfg file error
    [trident_leviathan_v1.2.cfg, voron2_leviathan_v1.2.cfg]
2024-07-23 fix typo in title block in voron2_leviathan_v1.2.cfg
    [voron2_leviathan_v1.2.cfg]
2024-07-31 update gear ratios
    [trident_leviathan_v1.2.cfg, voron2_leviathan_v1.2.cfg]
2024-08-02 update configure
    [trident_leviathan_v1.2.cfg]
2025-04-14 update cfg name
    [trident_leviathan.cfg, voron2_leviathan.cfg]
2025-05-06 Update README.md and add gitignore for KiCad directory
